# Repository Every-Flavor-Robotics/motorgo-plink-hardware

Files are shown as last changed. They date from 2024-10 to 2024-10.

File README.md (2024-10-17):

# MotorGo Plink
## The aim of this project is to make a 4 DC motor drive compatible with the motorgo ecosystem - specifically designed for beginner roboticists.  It should be the form factor of a pihat, but capable of operating entirely on it's own as well. Currently testing release version 1.0!
plink

### Feature list:
- Esp32s3 with Wifi and BT connectivity
- Form factor of a PiHat (we do not currently have the EEPROM requirements of the PiHat Spec)
- DC barrel jack and on-board buck from 6-17V into 5.1V up to 6A  (enough to power pi4 and pi5)
- 9 dof IMU  (LSM6DSOTR-C accel and gyro  +  LIS3MDLTR mag)
- USB-C programming compatible with arduino IDE
- Qwiic port x2 for easy integration with sensors
- Full gpio breakout on 40Pin header + full RPi GPIO passthrough if using as a hat
- 4 bidirectional DC motor channels up to 2A each channel
- 4 Encoder ports for use with EncoderGo 5pin jst for close loop feedback on each motor

### Schematics: 
- Top level


- Motor drivers


- IMU 


- Power system 


- connectors 


### Layout:
- Top - signals components and power


- Inner 1 - GND (I left faint top layer to show ground relative to traces)


- Inner 2 - GND and a tiny tiny power traces where needed


- Bottom - signals and power


- Dimensions


- Full




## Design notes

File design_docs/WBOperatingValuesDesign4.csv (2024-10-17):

Name | Value | Category | Description
Phase Marg | 59.51 ° | System Information | Bode Plot Phase Margin
Cross Freq | 55.92 kHz | System Information | Bode plot crossover frequency
Low Freq Gain | 72.57 dB | System Information | Gain at 1Hz
Gain Marg | -24.05 dB | System Information | Bode Plot Gain Margin
Vout | 5.09 V | System Information | Operational Output Voltage
IC Tolerance | 8 mV | IC | IC Feedback Tolerance
Cin IRMS | 2.79 A | Capacitor | Input capacitor RMS ripple current
Cin Pd | 2.59 mW | Capacitor | Input capacitor power dissipation
Cout IRMS | 371.57 mA | Capacitor | Output capacitor RMS ripple current
Cout Pd | 419.29 µW | Capacitor | Output capacitor power dissipation
Duty Cycle | 31.42% | System Information | Duty cycle
Efficiency | 90.5% | System Information | Steady state efficiency
Frequency | 881.05 kHz | System Information | Switching frequency
IC Tj | 112.33 °C | IC | IC junction temperature
ICThetaJA | 32 °C/W | IC | IC junction-to-ambient thermal resistance
L Ipp | 1.29 A | Inductor | Peak-to-peak inductor ripple current
L Pd | 630 mW | Inductor | Inductor power dissipation
IC Pd | 2.57 W | IC | IC power dissipation
Pout | 30.53 W | System Information | Total output power
Iin Avg | 1.98 A | IC | Average input current
IC Ipk | 6.64 A | IC | Peak switch current in IC
Mode | CCM | System Information | Conduction Mode
Vout p-p | 9.74 mV | System Information | Peak-to-peak output ripple voltage
M Irms | 3.36 A | Mosfet | MOSFET RMS current
Vout Ripple requirement used for Cout calculations | 3.00% | System Information | Custom maximum output ripple requirement that was used for Cout selection(% of Vout).
Vin p-p | 245.24 mV | System Information | Peak-to-peak input voltage
Vin Ripple requirement used for Cin calculations | 5.00% | System Information | Custom maximum input ripple requirement that was used for Cin selection(% of Minimum Vin).
Overshoot Value | 93.14 mV | System Information | Theoretical Vout Overshoot Value
Undershoot Value | 115.92 mV | System Information | Theoretical Vout Undershoot Value
Vout transient requirement used for Cout calculations | 5.00% | System Information | Custom Transient voltage change requirement that was used for Cout selection (% of Vout).
Iout transient step used for Cout calculations | 3 A | System Information | Custom Transient current step requirement that was used for Cout selection (A).
Minimum Cout required for stability | 17.75 uF | System Information | Minimum Cout required for stability
IC Iq Pd | 10.2 mW | IC | IC Iq Pd
Total Pd | 3.21 W | Power | Total Power Dissipation
FootPrint | 622 mm² | System Information | Total Foot Print Area of BOM components
Vin | 17 V | System Information | Vin operating point
Iout | 6 A | System Information | Iout operating point
Cin Pd | 2.59 mW | Power | Input capacitor power dissipation
Cout Pd | 419.29 µW | Power | Output capacitor power dissipation
L Pd | 630 mW | Power | Inductor power dissipation
IC Pd | 2.57 W | Power | IC power dissipation
Vout Actual | 5.09 V | System Information | Vout Actual calculated based on selected voltage divider resistors
Vout Tolerance | 2.72% | System Information | Vout Tolerance based on IC Tolerance (no load) and voltage divider resistors if applicable
Total BOM | $4.91 | System Information | Total BOM Cost
BOM Count | 17 | System Information | Total Design BOM count

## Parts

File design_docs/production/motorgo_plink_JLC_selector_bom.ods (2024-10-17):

Comment | topDesignator | bottomDesignator | Footprint | JLCPCB Part #
3.92k | R19 |  | Resistor_SMD:R_0402_1005Metric | C3013164
.022uF | C13,C5,C9 |  | Capacitor_SMD:C_0402_1005Metric | C1532
22uF16v | C24,C25 |  | Capacitor_SMD:C_0603_1608Metric | C2762594
0 | R6,R7 |  | Resistor_SMD:R_0402_1005Metric | C3017451
68pf | C1 |  | Capacitor_SMD:C_0201_0603Metric | C3833199
6.8nf | C20 |  | Capacitor_SMD:C_0201_0603Metric | C505476
BM05B-SRSS-TB_LF__SN_ | J14,J18,J16,J20 |  | SnapEDALibrary:JST_BM05B-SRSS-TB_LF__SN_ | C265092
53.6k | R24 |  | Resistor_SMD:R_0402_1005Metric | C2998086
47uF3mOhm | C23 |  | Capacitor_SMD:C_1210_3225Metric | C7432791
220uF50v | C16 |  | Capacitor_SMD:CP_Elec_10x10 | C125977
10k | R14,R10,R13,R36,R11,R12,R15,R37 |  | Resistor_SMD:R_0402_1005Metric | C25744
36.5k | R17 |  | Resistor_SMD:R_0402_1005Metric | C25887
LED | D2 |  | LED_SMD:LED_0805_2012Metric | C84260
TPS54620RHLR | U6 |  | LCSC_parts:VQFN-14_L3.5-W3.5-P0.50-TL-EP_TPS54622RHLT | C263274
USBLC6-2P6 | U2 |  | Package_TO_SOT_SMD:SOT-666 | C2827693
LED | D1 |  | LED_SMD:LED_0805_2012Metric | C84259
LED | D3 |  | LED_SMD:LED_0805_2012Metric | C84256
Conn_01x02_Pin | J8,J10,J22,J6 |  | Connector_Molex:Molex_KK-254_AE-6410-02A_1x02_P2.54mm_Vertical | C722716
4.7uF1mOhm | C17 |  | Capacitor_SMD:C_0603_1608Metric | C268021
tact_switch | J2,J3 |  | Button_Switch_SMD:SW_SPST_TL3342 | C2886897
ESP32-S3-WROOM-1 | U1 |  | mg_mini_v1r3:ESP32-S3-WROOM-1 | C2913198
DRV8874PWPR | U3,U9,U4,U5 |  | LCSC_parts:HTSSOP-16_L5.0-W4.4-P0.65-LS6.4-BL-EP | C1855818
LSM6DS3TR | U11 |  | LCSC_parts:LSM6DSOTR_LGA-14 | C967633
20k | RMODE3,RMODE2,RMODE1,RMODE4 |  | Resistor_SMD:R_0402_1005Metric | C3017501
10k | R25 |  | Resistor_SMD:R_0402_1005Metric | C2906885
.022uF | C28 |  | Capacitor_SMD:C_0402_1005Metric | C380305
1k | R50,R1,R49,R3,R46,R2 |  | Resistor_SMD:R_0402_1005Metric | C11702
2.2uH12.7mOhm | L1 |  | kicad_lceda:IND-SMD_L6.6-W6.4_CKSTT0610 | C5440776
100nF | C31,C22,C30 |  | Capacitor_SMD:C_0402_1005Metric | C880603
I2C_STANDARDQWIIC | J15,J13 |  | Connector_JST:JST_SH_BM04B-SRSS-TB_1x04-1MP_P1.00mm_Vertical | C495539
5k1 | R33,R31,R32,R9,R30,R4,R5,R8 |  | Resistor_SMD:R_0402_1005Metric | C25905
2k | R39,R38 |  | Resistor_SMD:R_0402_1005Metric | C4109
Conn_02x20_Odd_Even | J4 | J7 | Connector_PinSocket_2.54mm:PinSocket_2x20_P2.54mm_Vertical_SMD | C3975165
4.7uF1mOhm | C2,C19,C15 |  | Capacitor_SMD:C_0805_2012Metric | C440198
AMS1117-3.3 | U8 |  | Package_TO_SOT_SMD:SOT-223-3_TabPin2 | C347222
53.6k | R18 |  | Resistor_SMD:R_0402_1005Metric | C5153961
102k | R16 |  | Resistor_SMD:R_0402_1005Metric | C2933066
2.2nF0Ohm | C18 |  | Capacitor_SMD:C_0201_0603Metric | C5142540
1uF | C32 |  | Capacitor_SMD:C_0603_1608Metric | C15849
DC_Barrel | J11 |  | LCSC_parts:CONN-TH_DC-005-2.5A-2.0 | C84007
USB4520-03-0-A_REVA | J1 |  | mg_mini_v1r3:USB-C-SMD_TYPEC-303-ACP16 | C720628
100uF | C10,C6,C29,C14 |  | Capacitor_SMD:C_1210_3225Metric | C6120014
0.1uF | C26,C27,C11,C3,C4,C7,C12,C8 |  | Capacitor_SMD:C_0402_1005Metric | C307331
4.87k | RP1,RP4,RP3,RP2 |  | Resistor_SMD:R_0402_1005Metric | C3015971

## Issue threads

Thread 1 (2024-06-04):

Footprints wrong in BOM

alexchunlin, 2024-06-04:
R34 is the 0R0 to bridge the island of the IMU to the rest of the board and is selected as a 0402 resistor when the footprint is an 0603.
LCSC part number should be C3016185 or equivalent 0603 0Ohm resistor

J15, J17, J13, J19 are all the qwiic connectors and have vertical footprints, but the components chosen were for horizontal form.
LCSC part number should be C160390 - Part number: BM04B-SRSS-TB(LF)(SN)

Closed 2024-10-17.

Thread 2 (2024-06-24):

Pull nSleep HIGH on DRV8874

SwapnilPande, 2024-06-24:
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

Currently, nSleep is floating, it needs to be pulled HIGH to enable the motor controller

Closed 2024-10-17.

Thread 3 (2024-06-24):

IMU circuit errors

SwapnilPande, 2024-06-24:
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
* SDA/SCL switched for Magnetometer

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

Closed 2024-10-17.

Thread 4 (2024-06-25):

Raspberry Pi Pin headers are mirrored

SwapnilPande, 2024-06-25:

Closed 2024-10-17.

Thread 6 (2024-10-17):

add remove soldermask from around the mounting holes

alexchunlin, 2024-10-17:
Bottom of board has soldermask all the way up to the board holes.  It should match the design of the front of the board, where it is removed in a 5mm Diameter concentric on the hole.

alexchunlin, 2024-11-11:
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

bottom side matches now in diode rework branch

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

Closed 2024-11-11.

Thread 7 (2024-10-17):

sourcing 2x2 magnetometer challenges

alexchunlin, 2024-10-17:
the magnetometer chosen is not easy to source and might be considered to swap for a similar chip

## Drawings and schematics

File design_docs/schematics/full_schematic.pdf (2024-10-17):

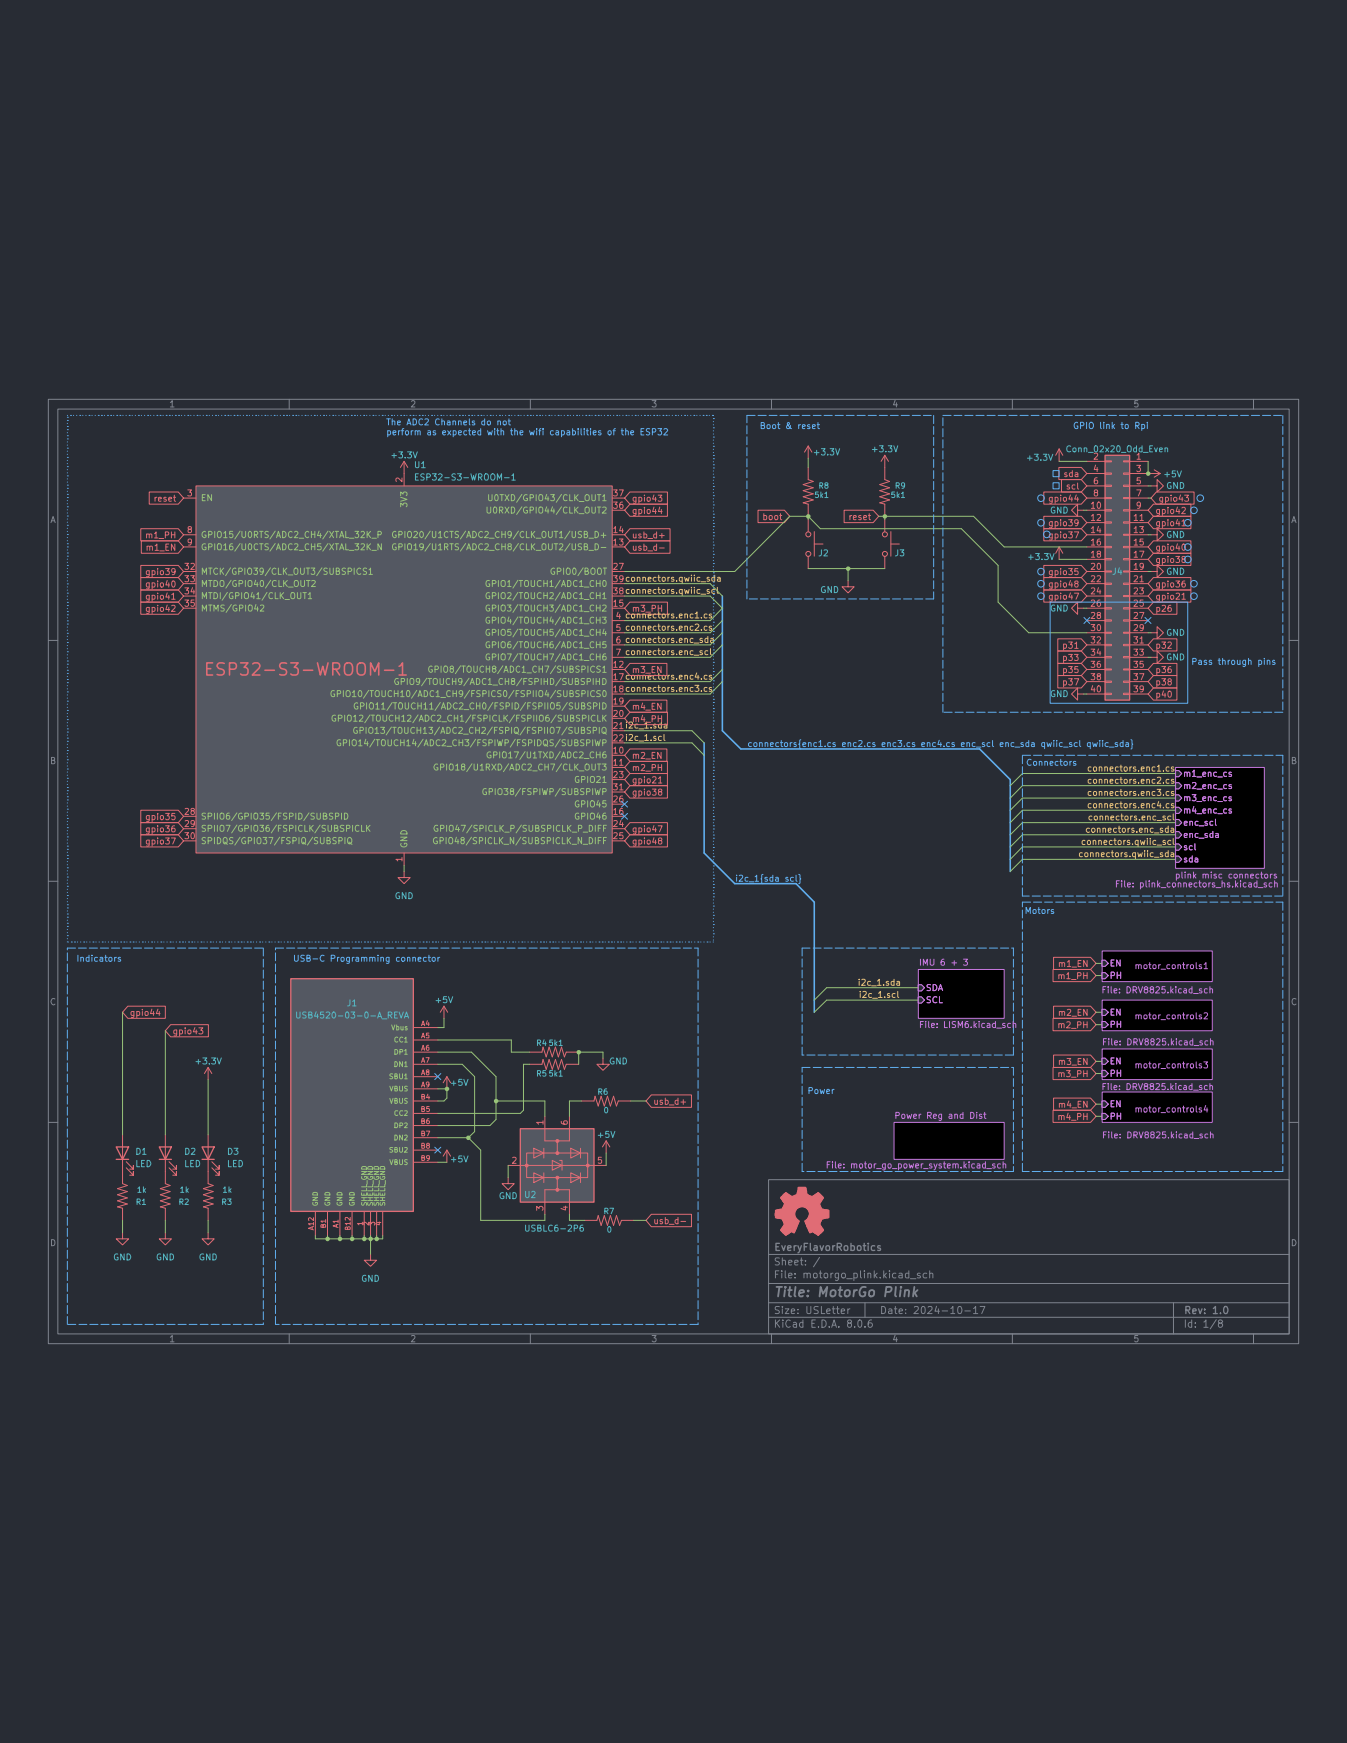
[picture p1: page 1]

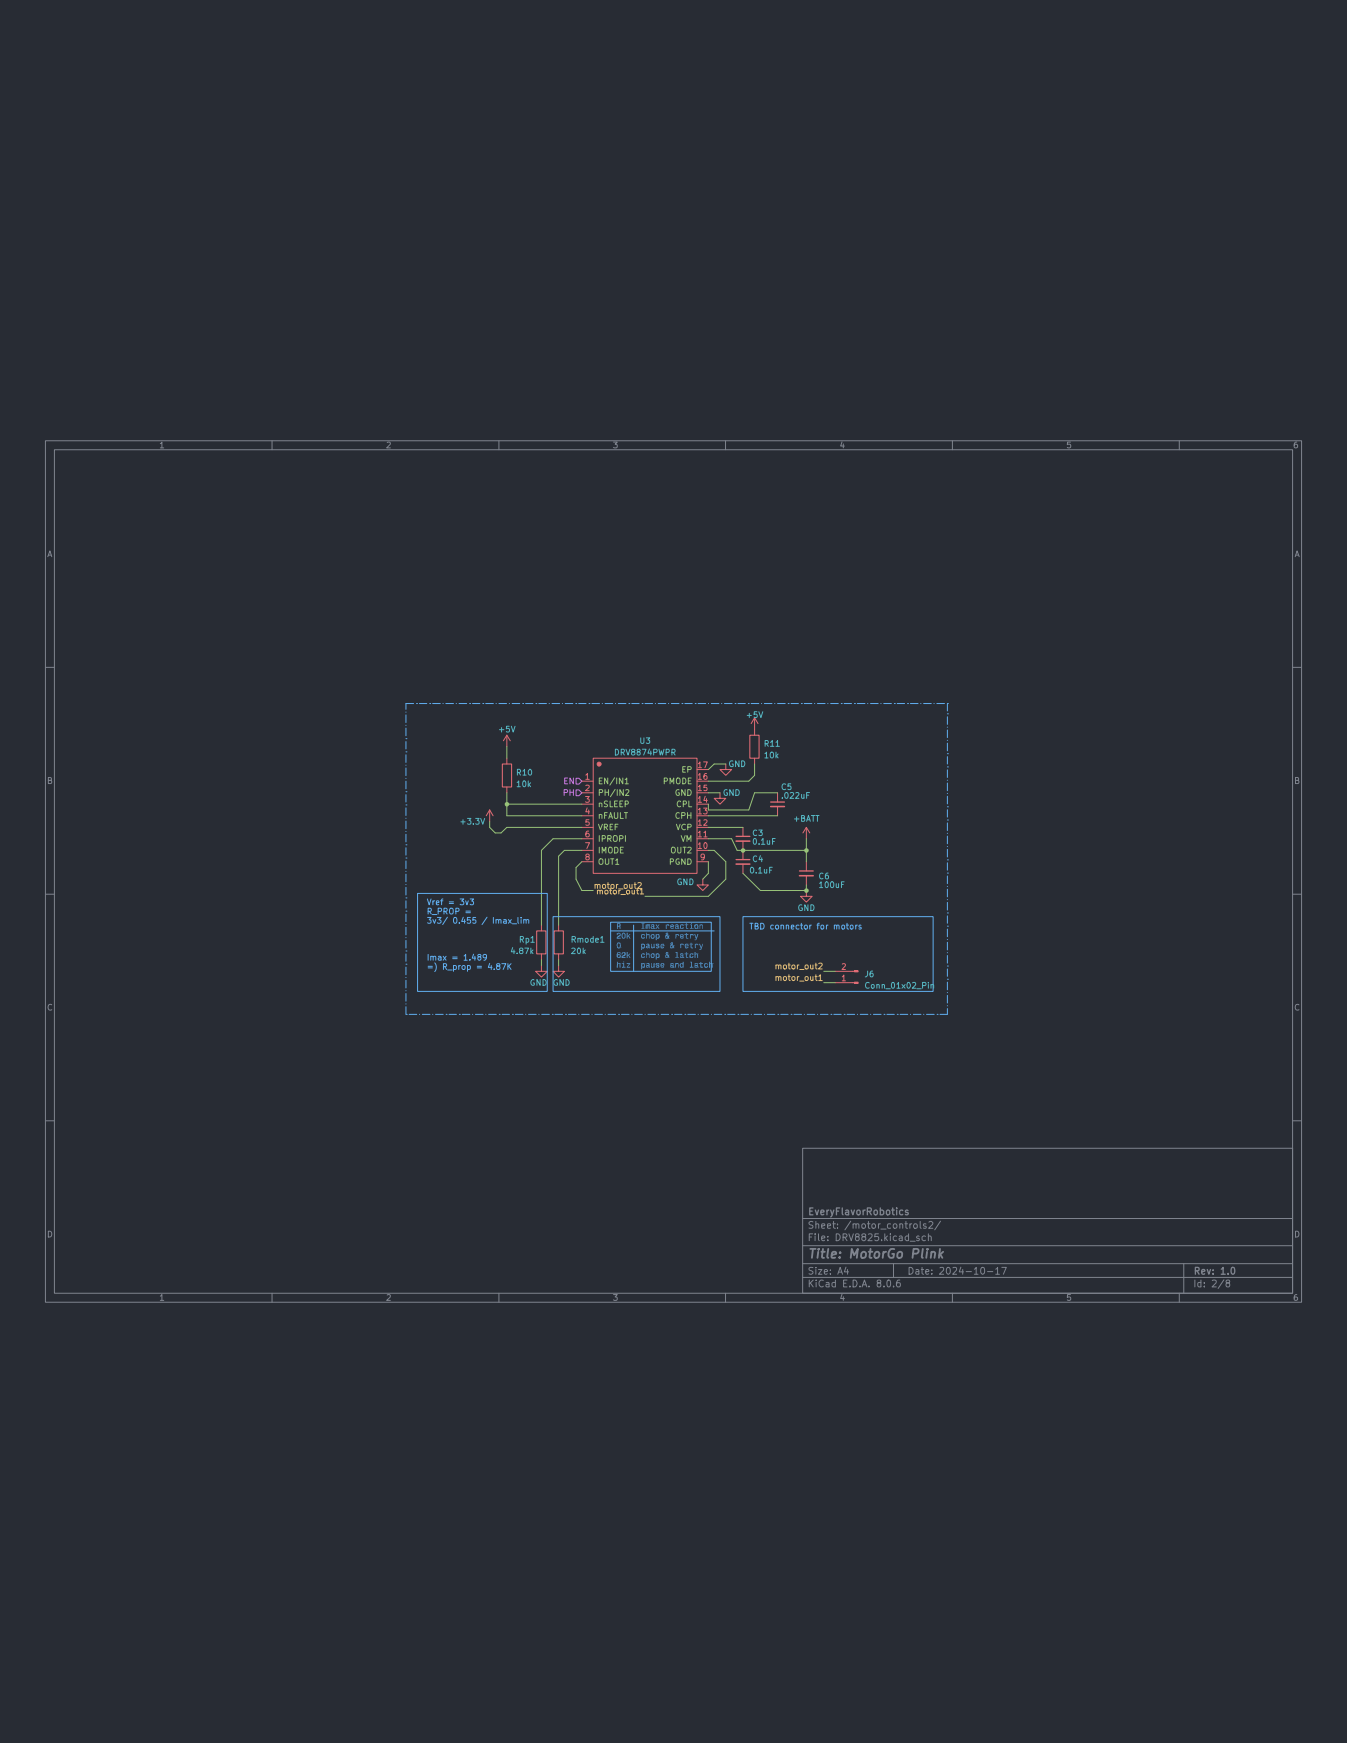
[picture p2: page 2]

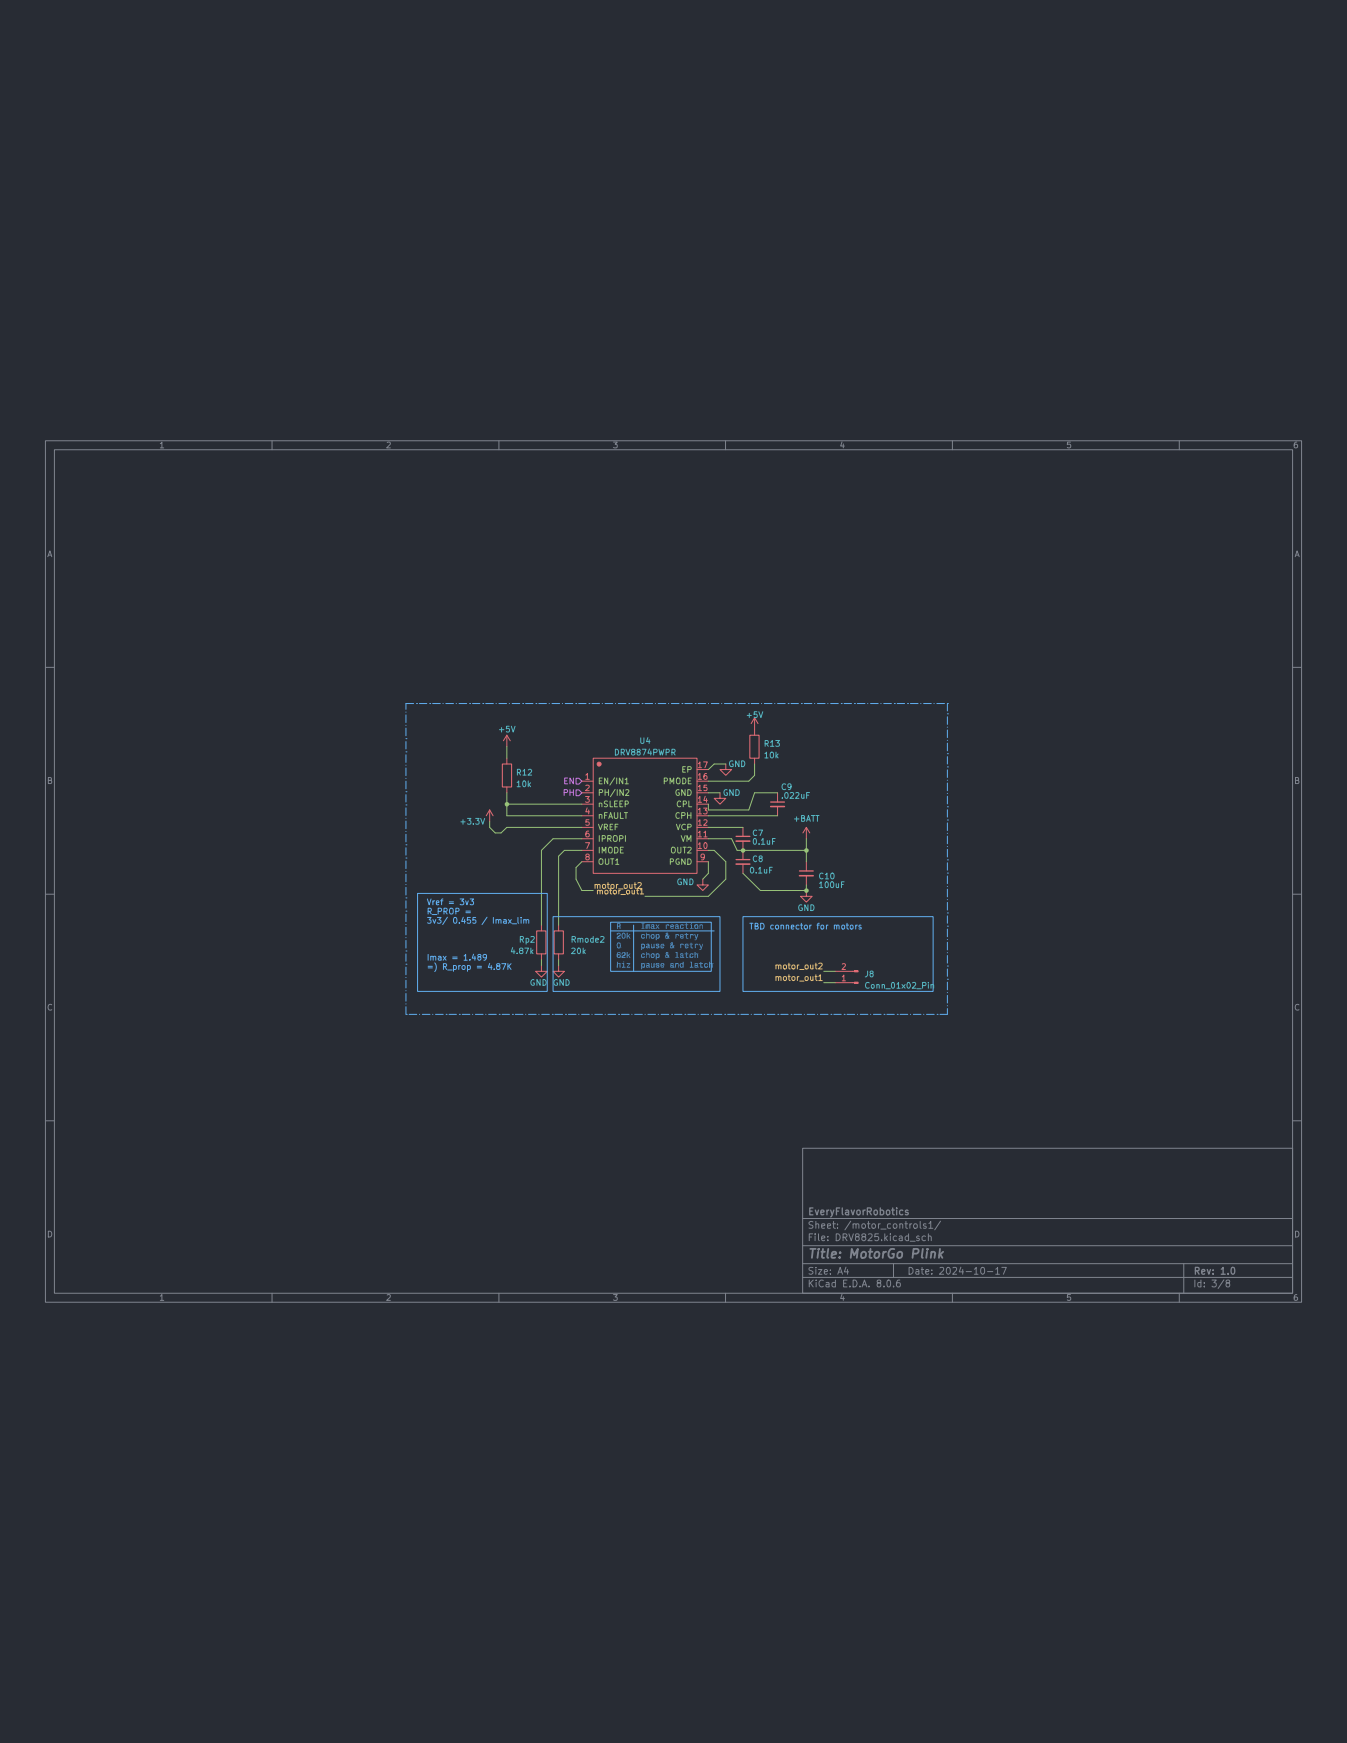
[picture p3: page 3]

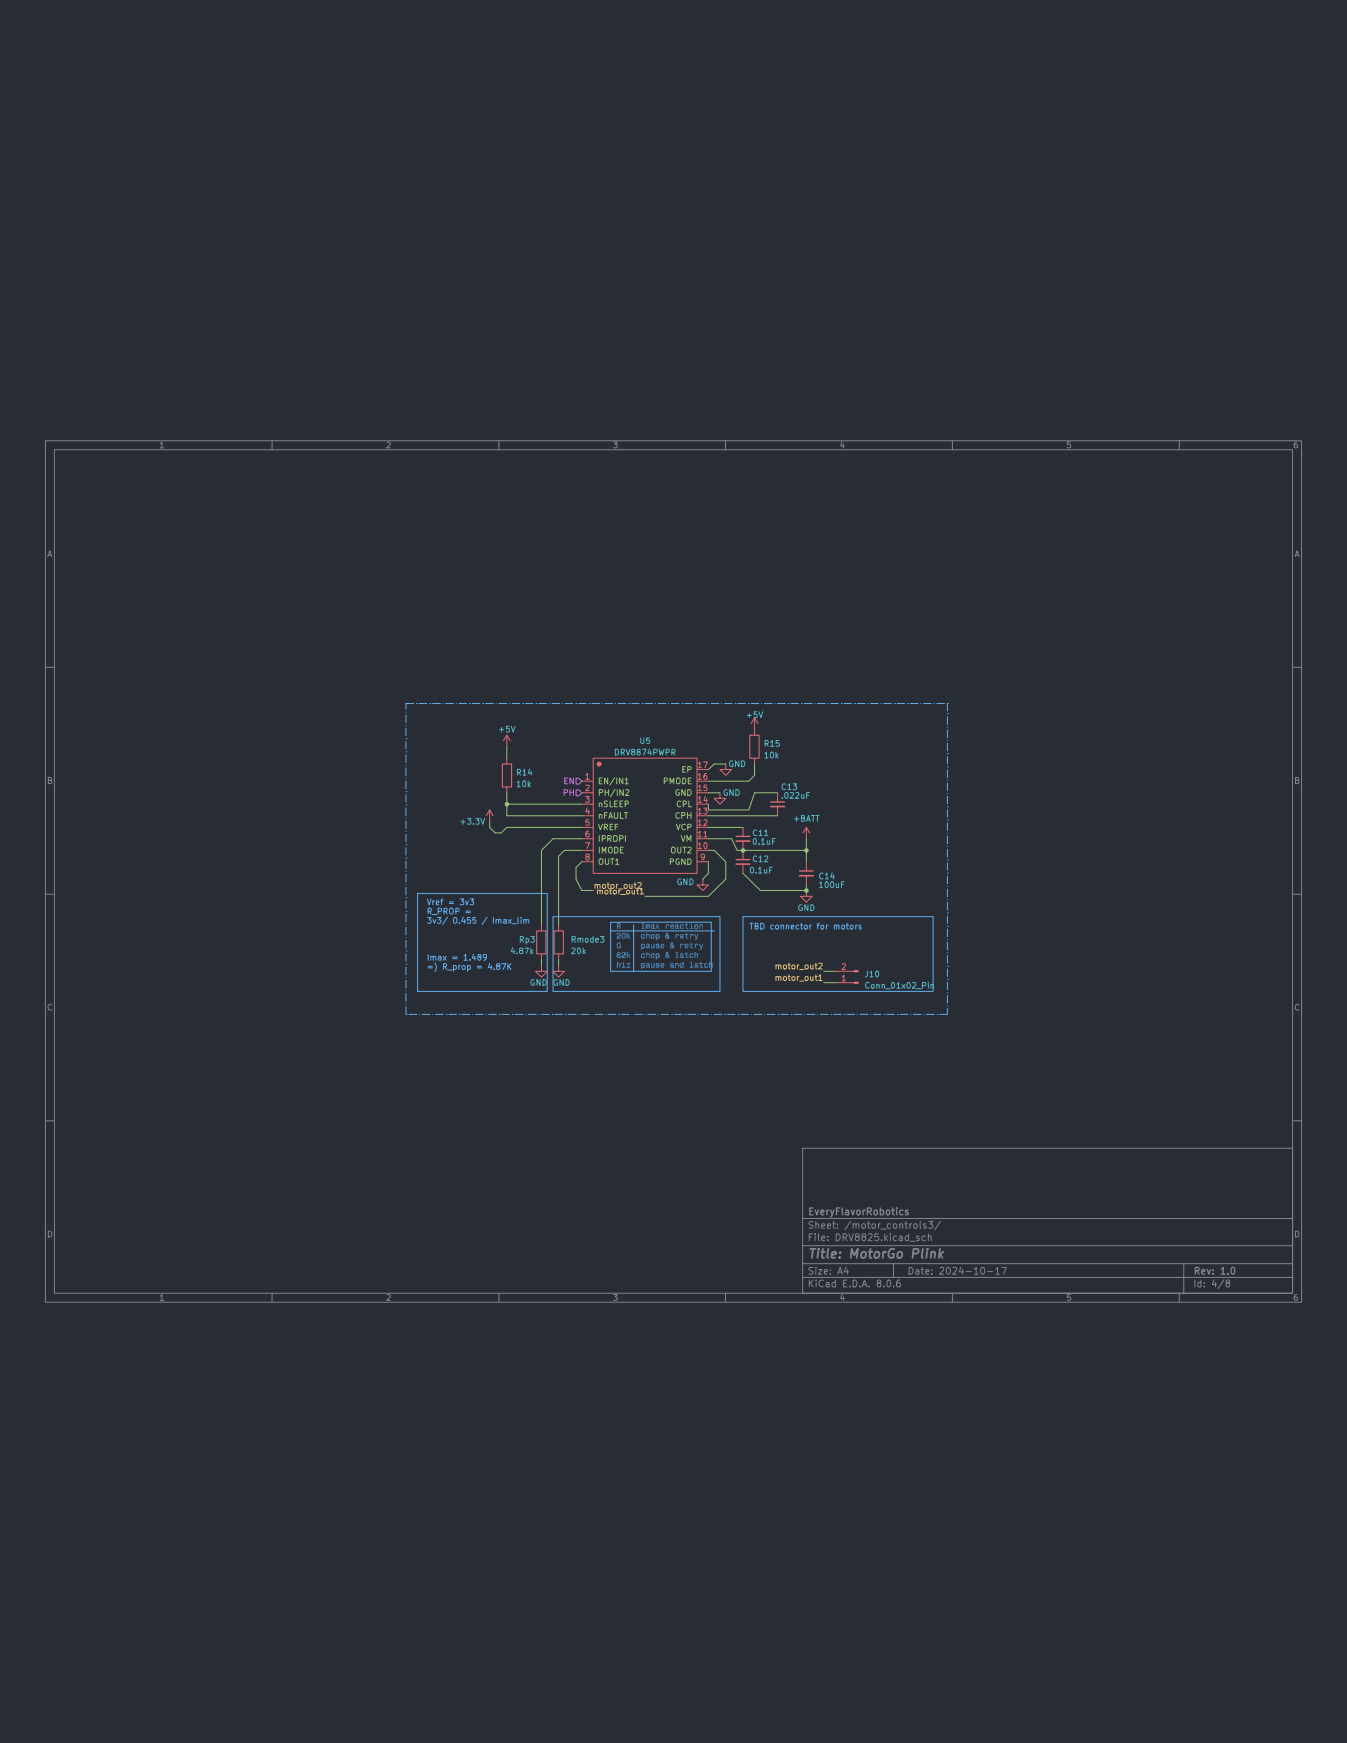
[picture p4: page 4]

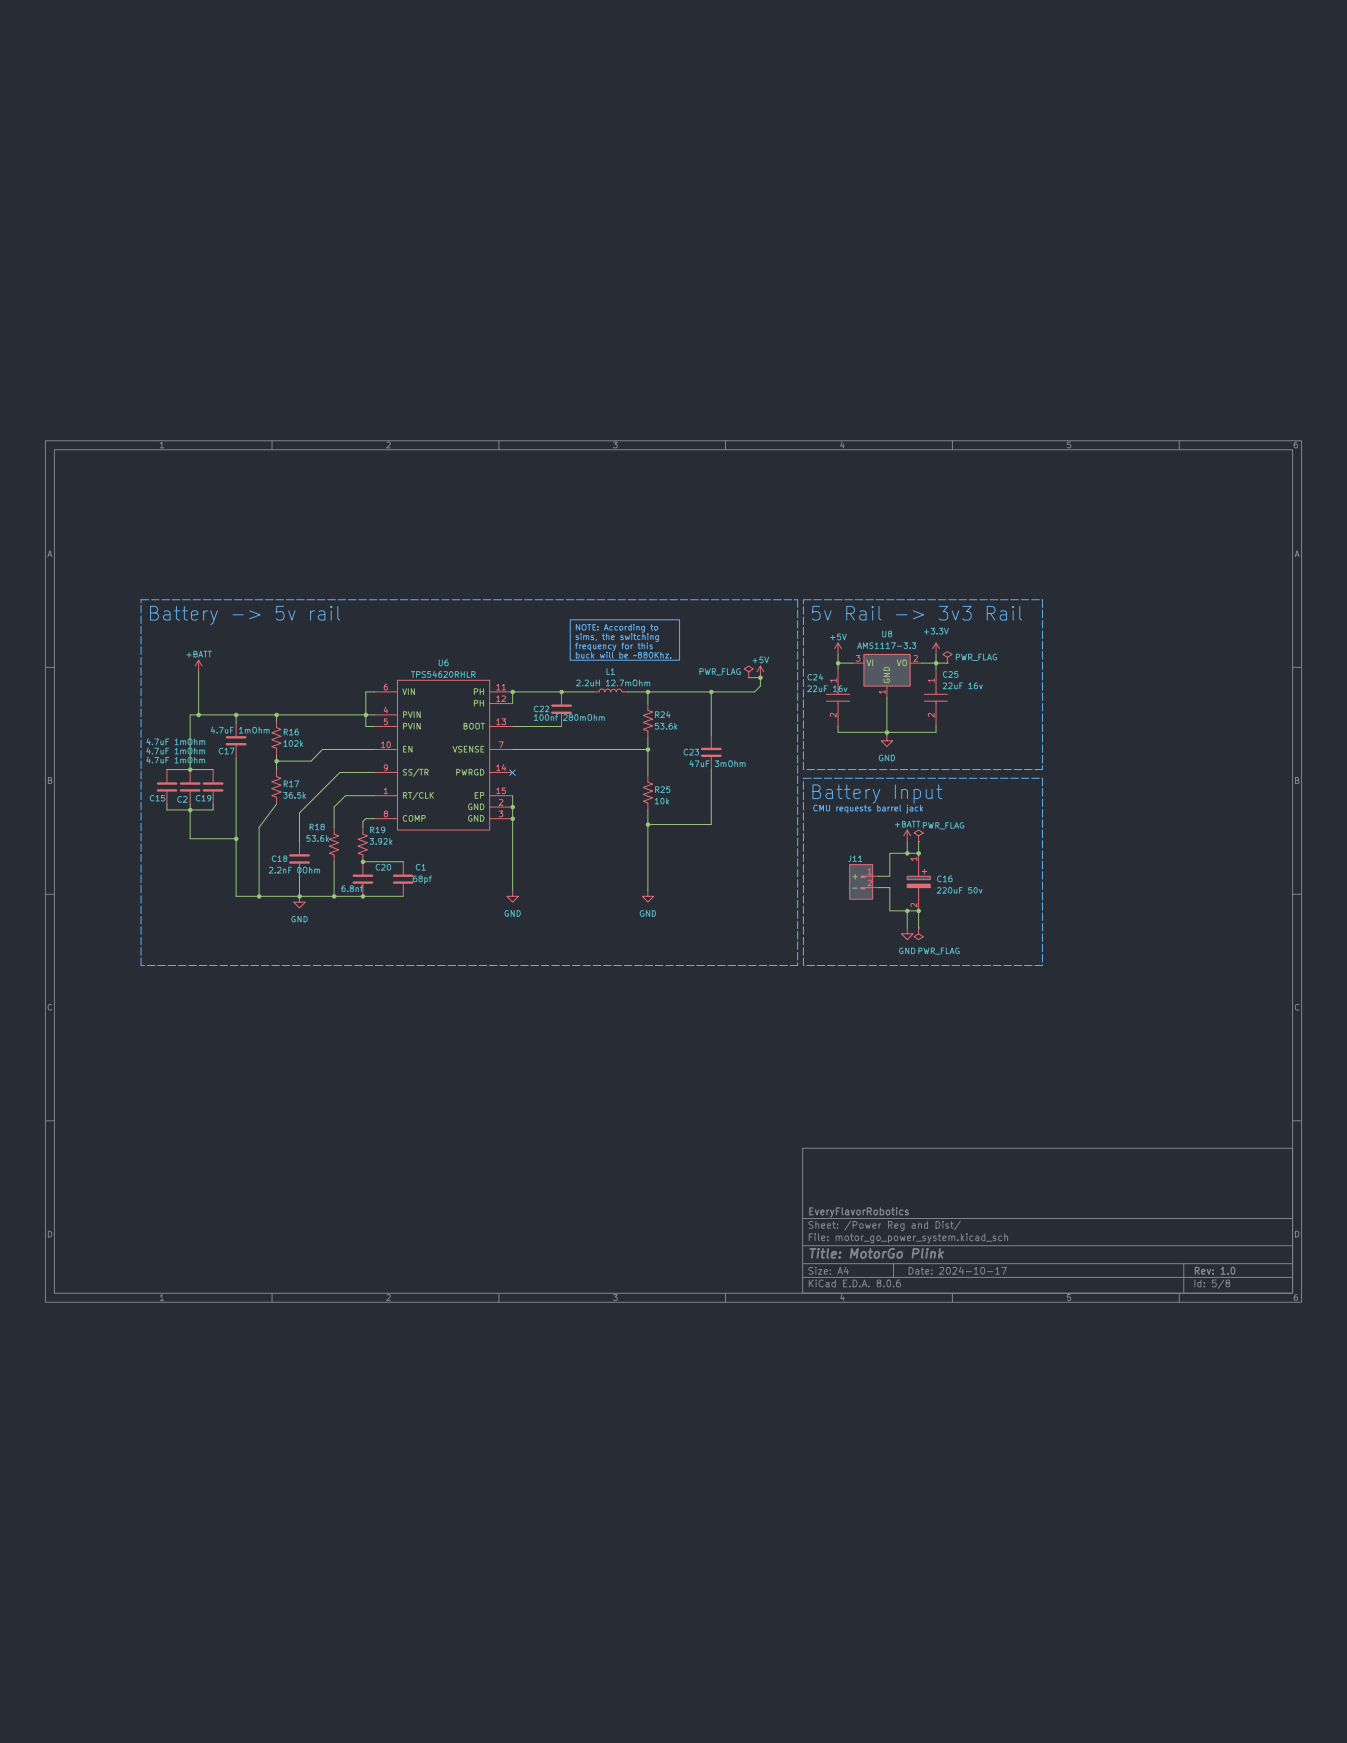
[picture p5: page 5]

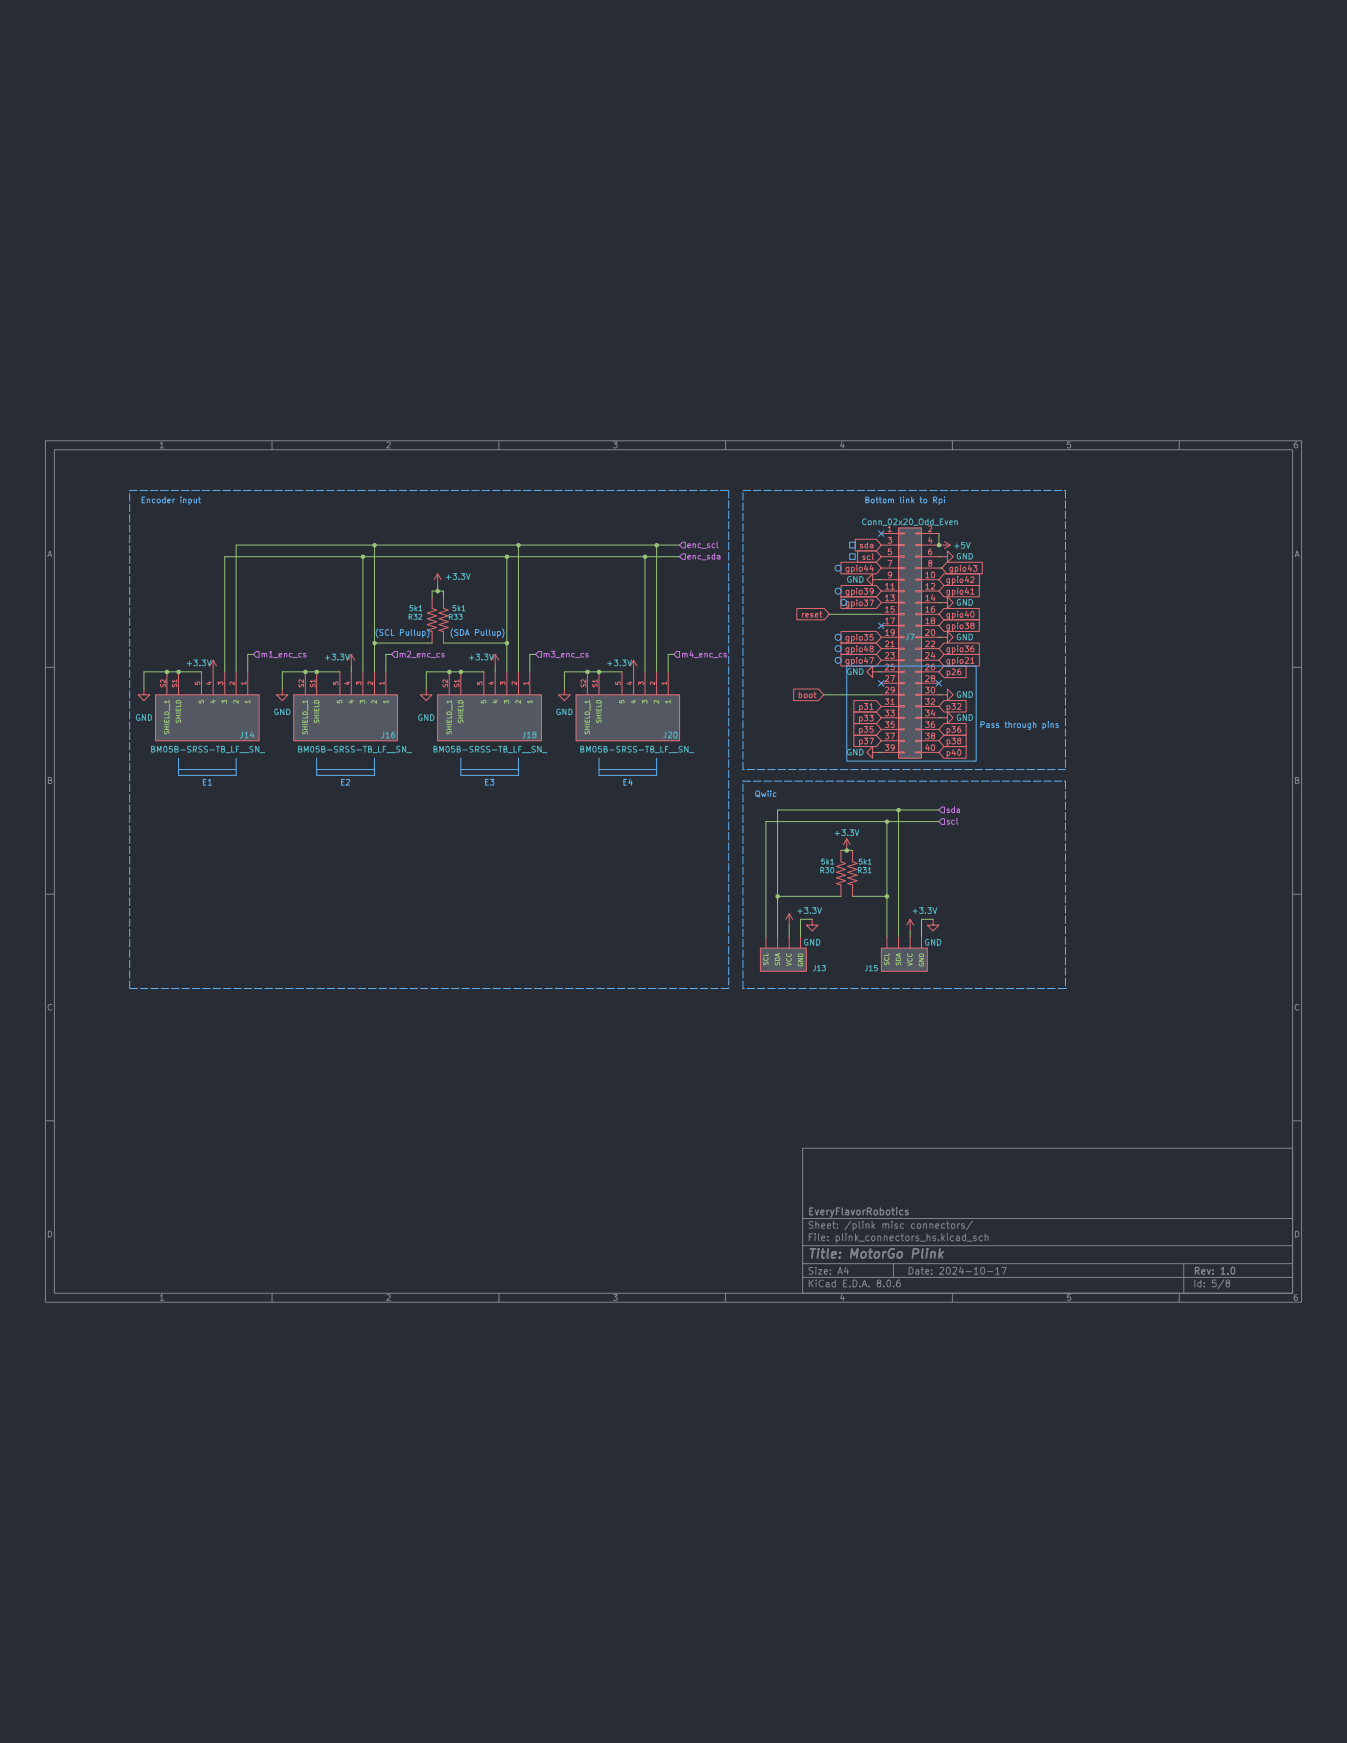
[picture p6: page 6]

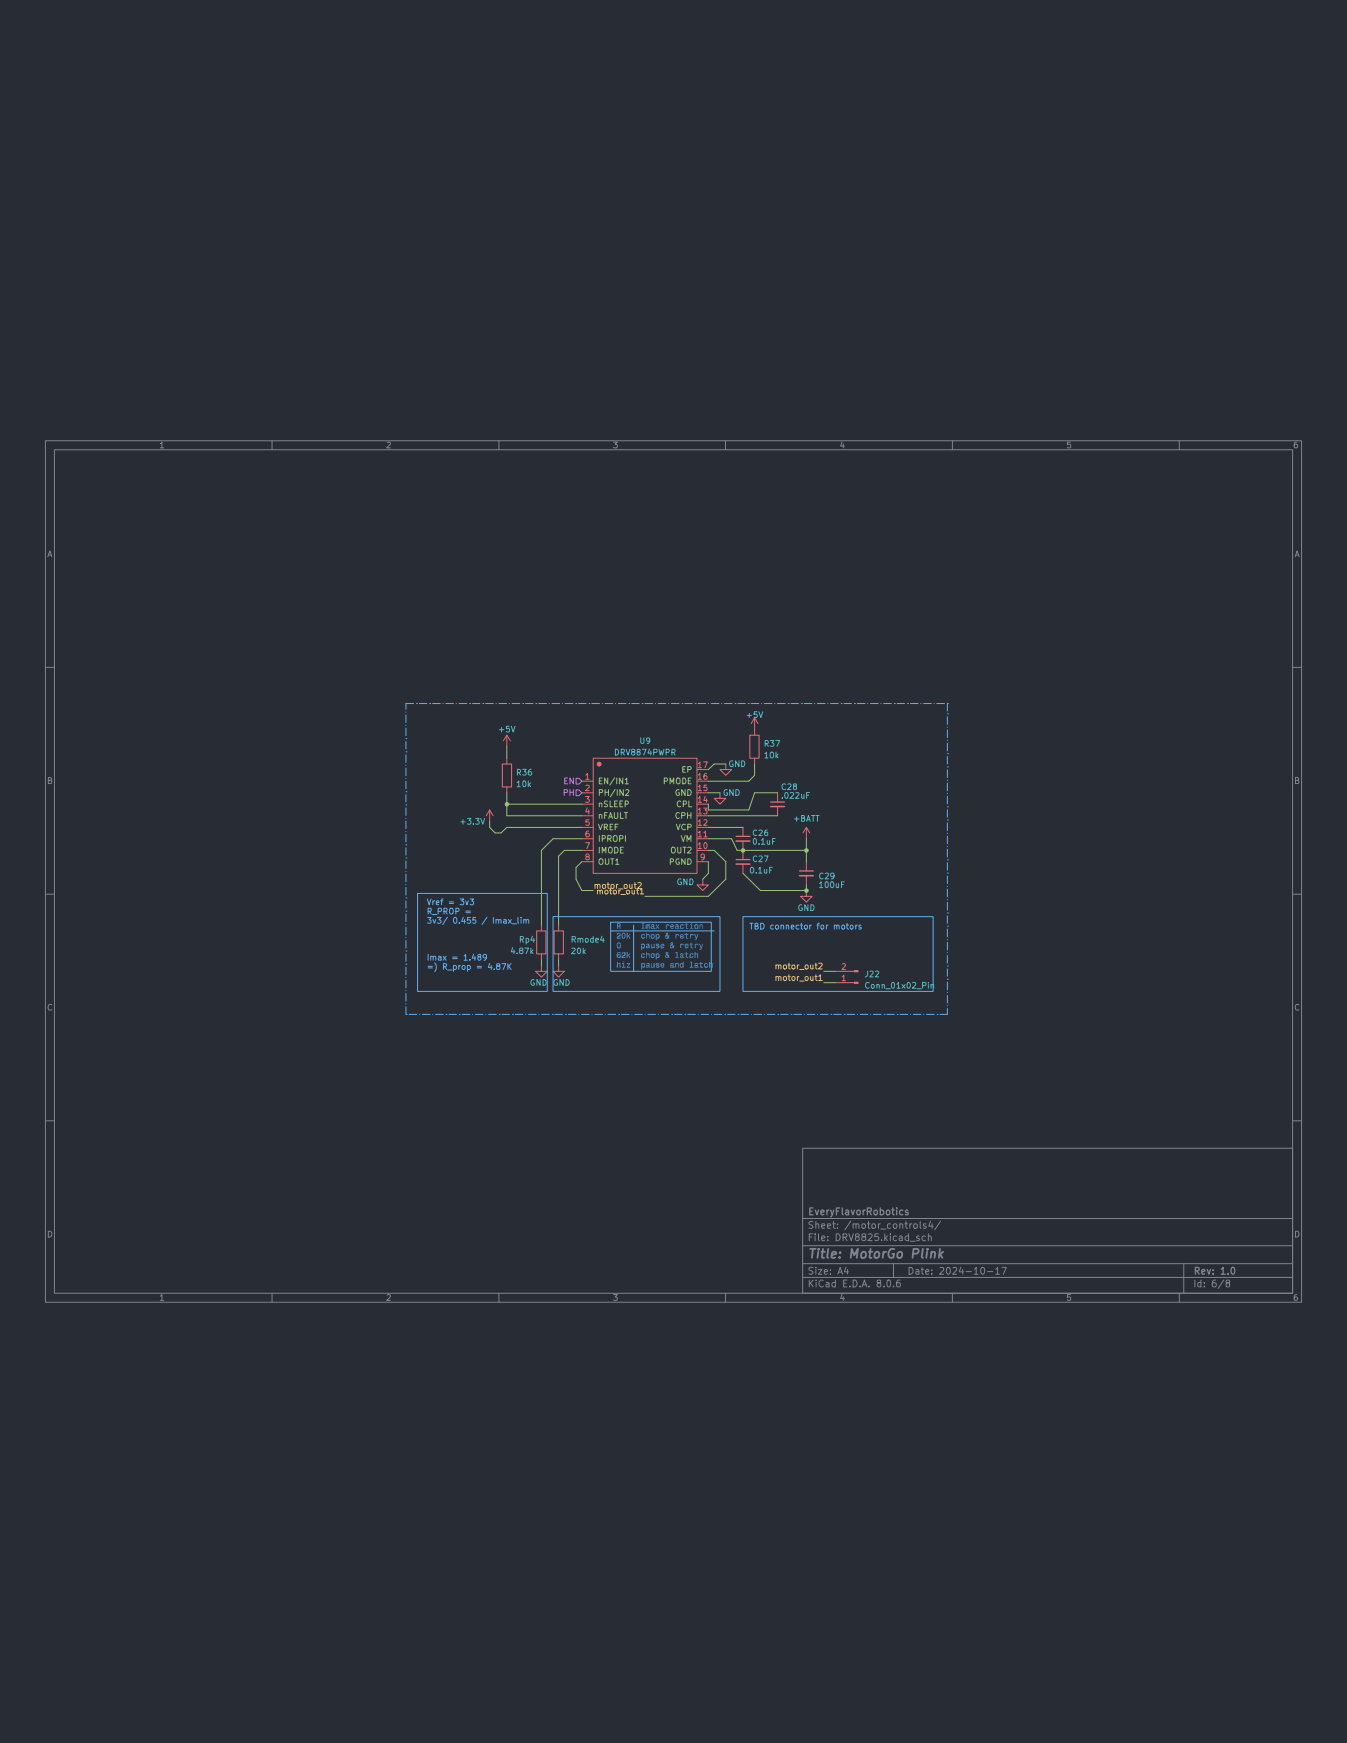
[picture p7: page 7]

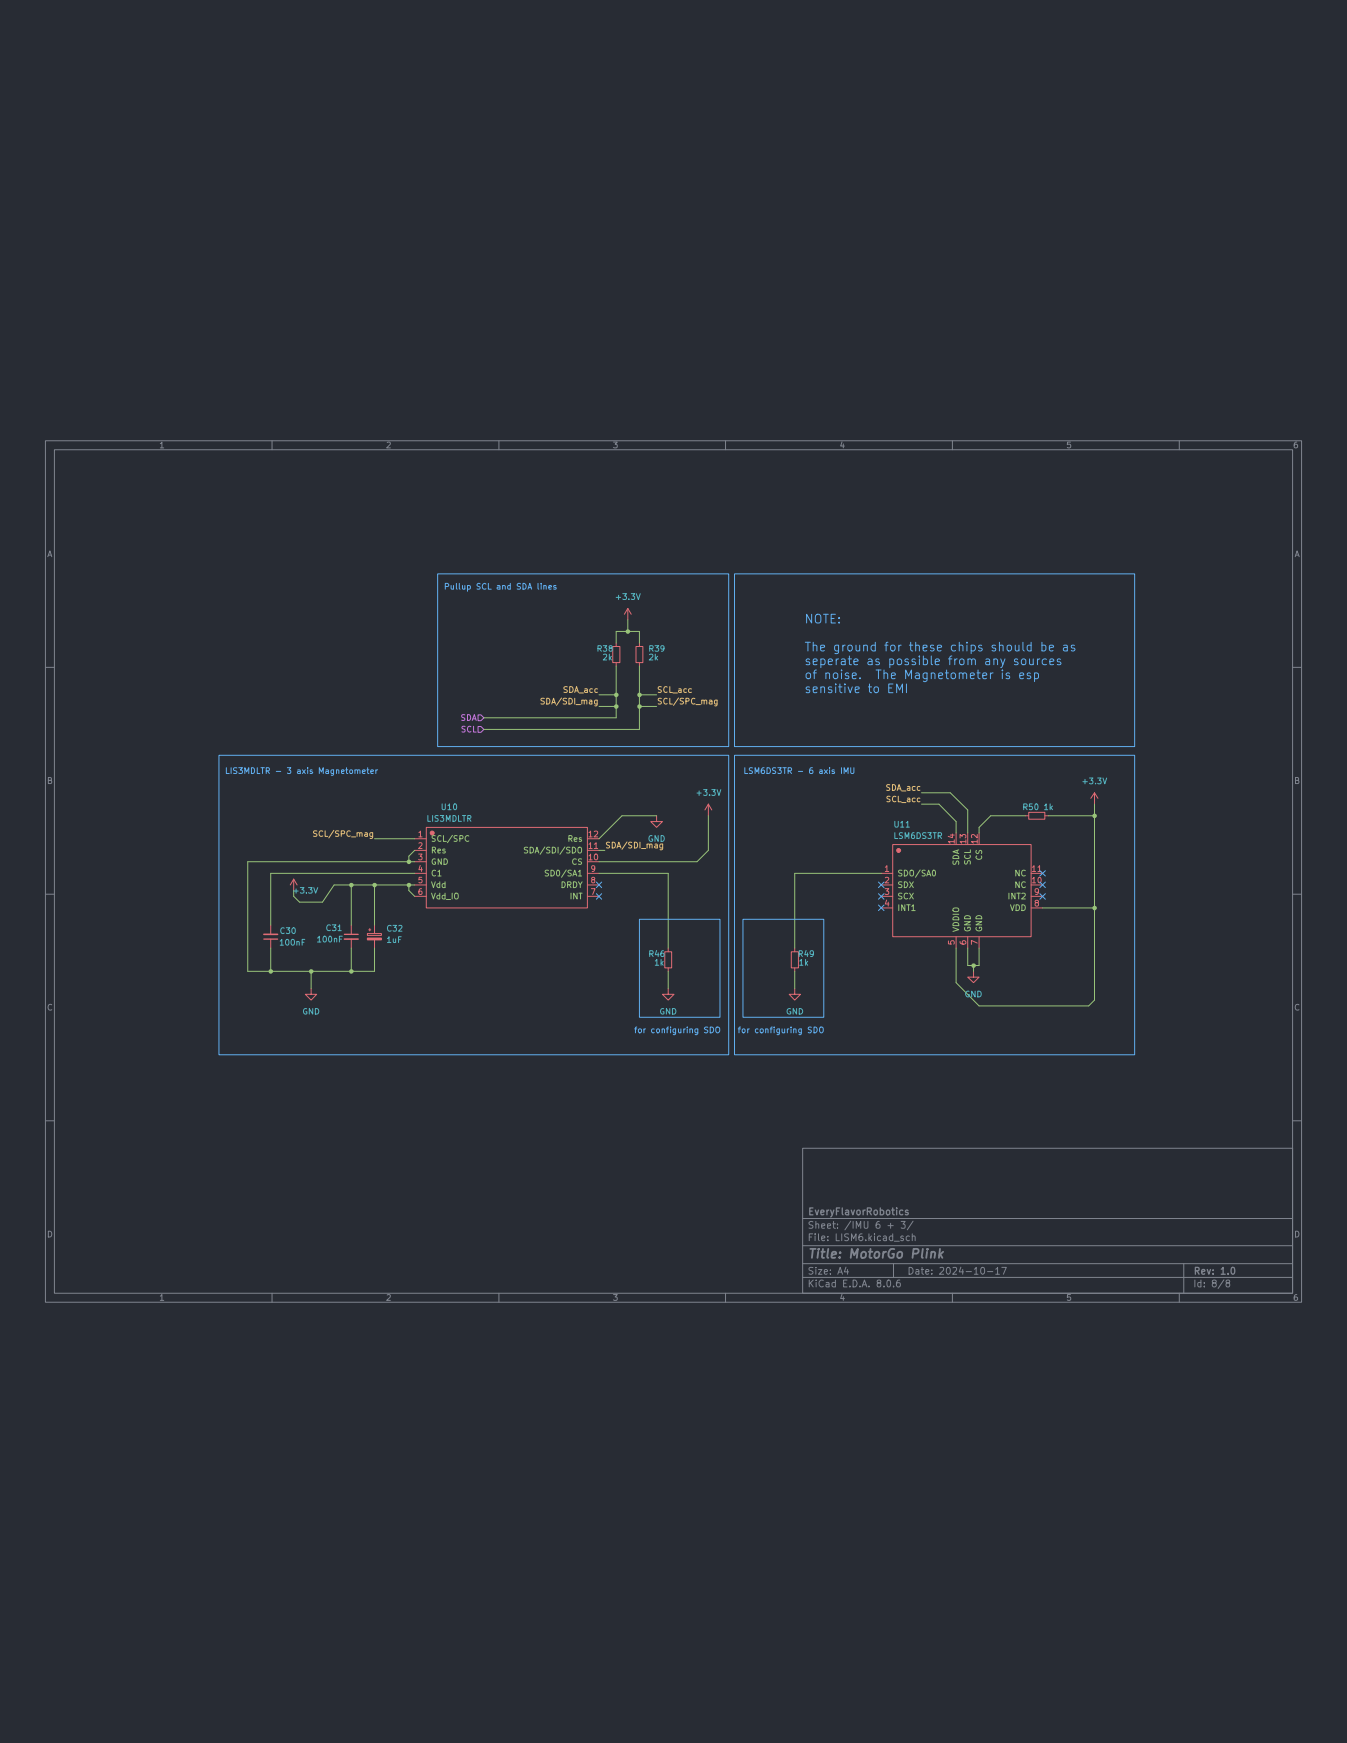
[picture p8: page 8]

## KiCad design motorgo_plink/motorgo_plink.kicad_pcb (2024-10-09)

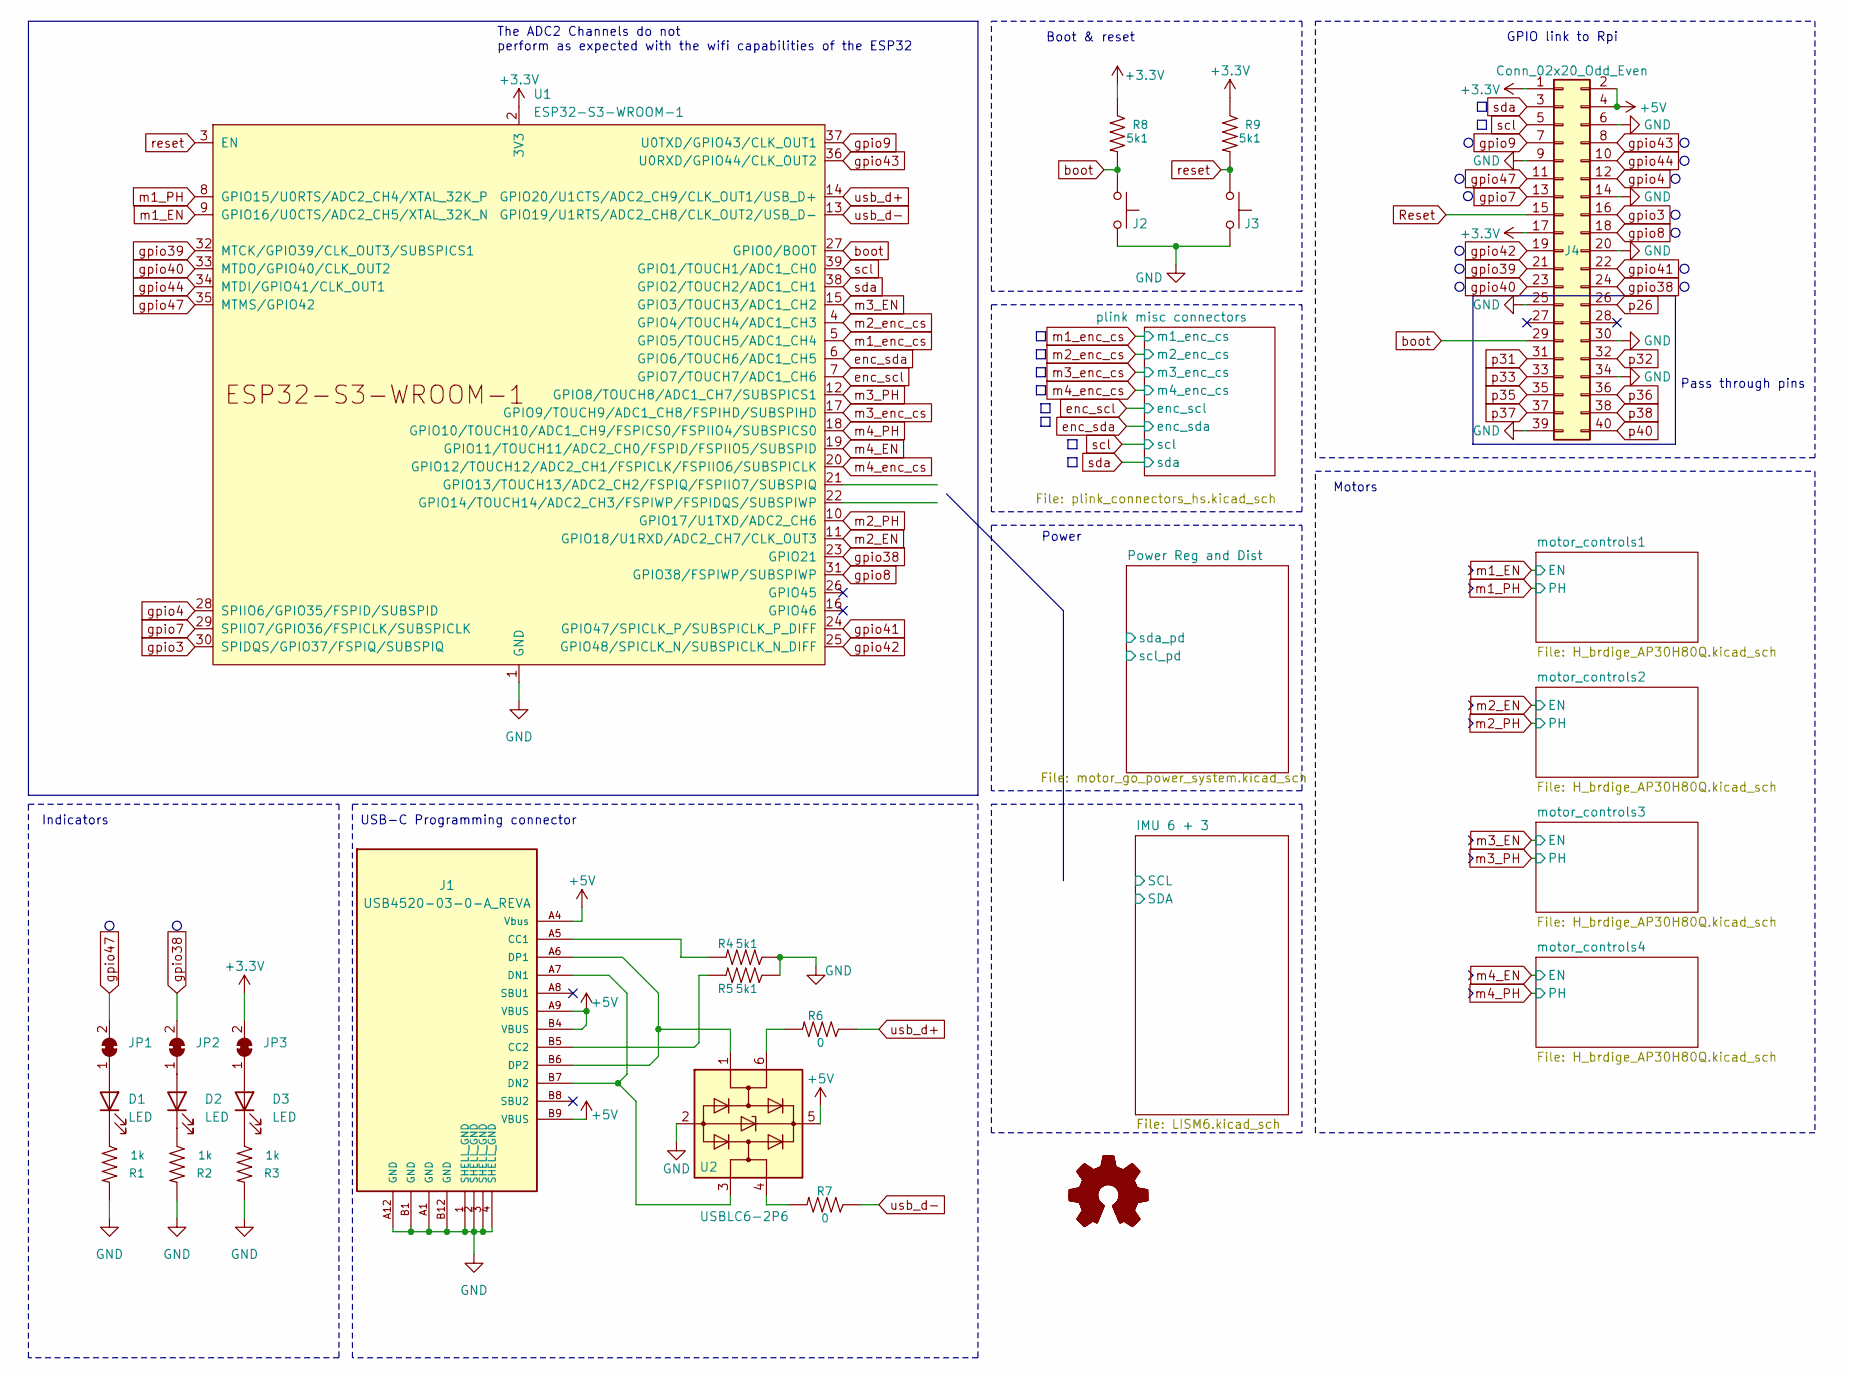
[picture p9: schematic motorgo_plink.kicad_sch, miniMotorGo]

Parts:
D1: LED; LED_0805_2012Metric; LCSC_Part_Number C84259
D2: LED; LED_0805_2012Metric; LCSC_Part_Number C84260
D3: LED; LED_0805_2012Metric; LCSC_Part_Number C84256
J1: USB4520-03-0-A_REVA; USB-C-SMD_TYPEC-303-ACP16; LCSC_Part_Number C720628
J2, J3: SW_SPST_TL3342; LCSC_Part_Number C2886897
J4: Conn_02x20_Odd_Even; PinSocket_2x20_P2.54mm_Vertical_SMD; LCSC_Part_Number C3975165
JP1, JP2, JP3: DNP; SolderJumper-2_P1.3mm_Open_RoundedPad1.0x1.5mm
R1, R2, R3: 1k; R_0402_1005Metric; LCSC_Part_Number C2906899
R4, R5, R8, R9: 5k1; R_0402_1005Metric; LCSC_Part_Number C409700
R6, R7: 0; R_0402_1005Metric; LCSC_Part_Number C3017451
U1: ESP32-S3-WROOM-1; LCSC_Part_Number C2913198
U2: USBLC6-2P6; SOT-666; LCSC_Part_Number C2827693

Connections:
+3.3V: J4.1, J4.17, JP3.2 (B), R8.1, R9.1, U1.2 (3V3); also elsewhere on the board
+5V: J1.A4 (Vbus), J1.A9 (VBUS), J1.B4 (VBUS), J1.B9 (VBUS), J4.2, J4.4, U2.5 (VBUS); also elsewhere on the board
GND: J1.1 (SHELL_GND), J1.2 (SHELL_GND), J1.3 (SHELL_GND), J1.4 (SHELL_GND), J1.A1 (GND), J1.A12 (GND), J1.B1 (GND), J1.B12 (GND), J2.1, J3.2, J4.6, J4.9, J4.14, J4.20, J4.25, J4.30, J4.34, J4.39, R1.2, R2.2, R3.2, R4.1, R5.1, U1.1 (GND), U1.40 (GND), U1.41 (GND), U2.2 (GND); also elsewhere on the board
unnamed: D1.2 (A), JP1.1 (A)
unnamed: D1.1 (K), R1.1
unnamed: D2.2 (A), JP2.1 (A)
unnamed: D2.1 (K), R2.1
unnamed: D3.2 (A), JP3.1 (A)
unnamed: D3.1 (K), R3.1
unnamed: J1.A5 (CC1), R4.2
unnamed: J1.B5 (CC2), R5.2
unnamed: J1.A7 (DN1), J1.B7 (DN2), U2.3 (I/O2)
unnamed: J1.A6 (DP1), J1.B6 (DP2), U2.1 (I/O1)
unnamed: R6.2, U2.6 (I/O1)
unnamed: R7.2, U2.4 (I/O2)
Reset: J4.15; also elsewhere on the board
boot: J2.2, J4.29, R8.2, U1.27 (GPIO0/BOOT); also elsewhere on the board
enc_scl: U1.7 (GPIO7/TOUCH7/ADC1_CH6); also elsewhere on the board
enc_sda: U1.6 (GPIO6/TOUCH6/ADC1_CH5); also elsewhere on the board
gpio3: J4.16, U1.30 (SPIDQS/GPIO37/FSPIQ/SUBSPIQ); also elsewhere on the board
gpio4: J4.12, U1.28 (SPIIO6/GPIO35/FSPID/SUBSPID); also elsewhere on the board
gpio7: J4.13, U1.29 (SPIIO7/GPIO36/FSPICLK/SUBSPICLK); also elsewhere on the board
gpio8: J4.18, U1.31 (GPIO38/FSPIWP/SUBSPIWP); also elsewhere on the board
gpio9: J4.7, U1.37 (U0TXD/GPIO43/CLK_OUT1); also elsewhere on the board
gpio38: J4.24, JP2.2 (B), U1.23 (GPIO21); also elsewhere on the board
gpio39: J4.21, U1.32 (MTCK/GPIO39/CLK_OUT3/SUBSPICS1); also elsewhere on the board
gpio40: J4.23, U1.33 (MTDO/GPIO40/CLK_OUT2); also elsewhere on the board
gpio41: J4.22, U1.24 (GPIO47/SPICLK_P/SUBSPICLK_P_DIFF); also elsewhere on the board
gpio42: J4.19, U1.25 (GPIO48/SPICLK_N/SUBSPICLK_N_DIFF); also elsewhere on the board
gpio43: J4.8, U1.36 (U0RXD/GPIO44/CLK_OUT2); also elsewhere on the board
gpio44: J4.10, U1.34 (MTDI/GPIO41/CLK_OUT1); also elsewhere on the board
gpio47: J4.11, JP1.2 (B), U1.35 (MTMS/GPIO42); also elsewhere on the board
hidden_scl: U1.22 (GPIO14/TOUCH14/ADC2_CH3/FSPIWP/FSPIDQS/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); also elsewhere on the board
hidden_sda: U1.21 (GPIO13/TOUCH13/ADC2_CH2/FSPIQ/FSPIIO7/S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); also elsewhere on the board
m1_EN: U1.9 (GPIO16/U0CTS/ADC2_CH5/XTAL_32K_N); also elsewhere on the board
m1_PH: U1.8 (GPIO15/U0RTS/ADC2_CH4/XTAL_32K_P); also elsewhere on the board
m1_enc_cs: U1.5 (GPIO5/TOUCH5/ADC1_CH4); also elsewhere on the board
m2_EN: U1.11 (GPIO18/U1RXD/ADC2_CH7/CLK_OUT3); also elsewhere on the board
m2_PH: U1.10 (GPIO17/U1TXD/ADC2_CH6); also elsewhere on the board
m2_enc_cs: U1.4 (GPIO4/TOUCH4/ADC1_CH3); also elsewhere on the board
m3_EN: U1.15 (GPIO3/TOUCH3/ADC1_CH2); also elsewhere on the board
m3_PH: U1.12 (GPIO8/TOUCH8/ADC1_CH7/SUBSPICS1); also elsewhere on the board
m3_enc_cs: U1.17 (GPIO9/TOUCH9/ADC1_CH8/FSPIHD/SUBSPIHD); also elsewhere on the board
m4_EN: U1.19 (GPIO11/TOUCH11/ADC2_CH0/FSPID/FSPIIO5/S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); also elsewhere on the board
m4_PH: U1.18 (GPIO10/TOUCH10/ADC1_CH9/FSPICS0/FSPIIO4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); also elsewhere on the board
m4_enc_cs: U1.20 (GPIO12/TOUCH12/ADC2_CH1/FSPICLK/FSPIIO6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); also elsewhere on the board
p26: J4.26; also elsewhere on the board
p31: J4.31; also elsewhere on the board
p32: J4.32; also elsewhere on the board
p33: J4.33; also elsewhere on the board
p35: J4.35; also elsewhere on the board
p36: J4.36; also elsewhere on the board
p37: J4.37; also elsewhere on the board
p38: J4.38; also elsewhere on the board
p40: J4.40; also elsewhere on the board
reset: J3.1, R9.2, U1.3 (EN)
scl: J4.5, U1.39 (GPIO1/TOUCH1/ADC1_CH0); also elsewhere on the board
sda: J4.3, U1.38 (GPIO2/TOUCH2/ADC1_CH1); also elsewhere on the board
usb_d+: R6.1, U1.14 (GPIO20/U1CTS/ADC2_CH9/CLK_OUT1/USB_D+)
usb_d-: R7.1, U1.13 (GPIO19/U1RTS/ADC2_CH8/CLK_OUT2/USB_D-)

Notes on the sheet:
USB-C Programming connector
Motors
Power
Boot & reset
Indicators
The ADC2 Channels do not perform as expected with the wifi capabilities of the ESP32
Pass through pins
GPIO link to Rpi

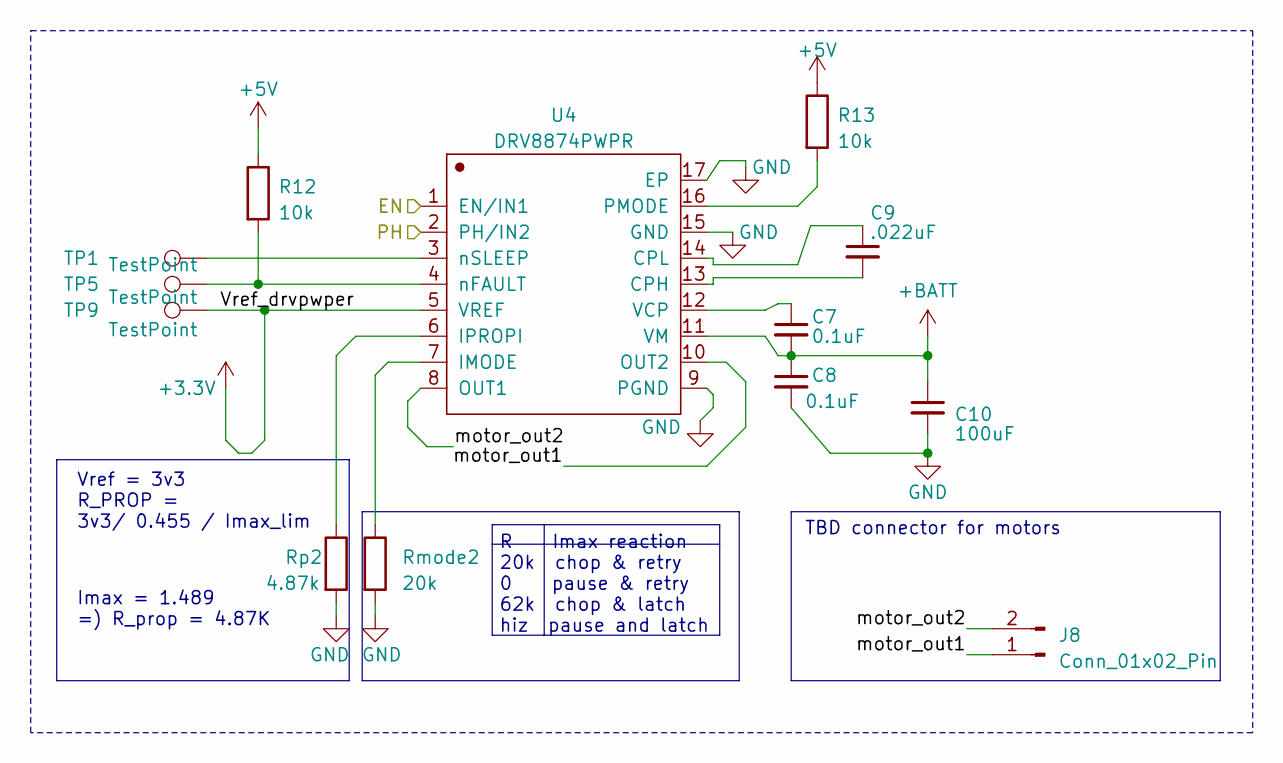
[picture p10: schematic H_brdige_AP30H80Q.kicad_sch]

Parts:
C7, C8: 0.1uF; C_0402_1005Metric; LCSC_Part_Number C3012377
C9: .022uF; C_0402_1005Metric; LCSC_Part_Number C380305
C10: 100uF; C_1210_3225Metric; LCSC_Part_Number C6120014
J8: Conn_01x02_Pin; PinHeader_1x02_P2.54mm_Vertical; LCSC_Part_Number C7430358
R12, R13: 10k; R_0402_1005Metric; LCSC_Part_Number C2906885
Rmode2: 20k; R_0402_1005Metric; LCSC_Part_Number C3017501
Rp2: 4.87k; R_0402_1005Metric; LCSC_Part_Number C3015971
TP1, TP5, TP9: TestPoint; TestPoint_Pad_1.0x1.0mm
U4: DRV8874PWPR; HTSSOP-16_L5.0-W4.4-P0.65-LS6.4-BL-EP; LCSC_Part_Number C1855818

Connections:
+3.3V: TP9.1, U4.5 (VREF); also elsewhere on the board
+5V: R12.1, R13.1; also elsewhere on the board
+BATT: C7.2, C8.1, C10.1, U4.11 (VM); also elsewhere on the board
/motor_controls1/motor_out1: J8.1, U4.10 (OUT2)
/motor_controls1/motor_out2: J8.2, U4.8 (OUT1)
GND: C8.2, C10.2, Rmode2.2, Rp2.2, U4.9 (PGND), U4.15 (GND), U4.17 (EP); also elsewhere on the board
unnamed: C9.2, U4.13 (CPH)
unnamed: C9.1, U4.14 (CPL)
unnamed: Rmode2.1, U4.7 (IMODE)
unnamed: Rp2.1, U4.6 (IPROPI)
unnamed: R13.2, U4.16 (PMODE)
unnamed: C7.1, U4.12 (VCP)
m1_EN: U4.1 (EN/IN1); also elsewhere on the board
m1_PH: U4.2 (PH/IN2); also elsewhere on the board

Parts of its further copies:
C3, C4, C11, C12, C26, C27: 0.1uF; C_0402_1005Metric; LCSC_Part_Number C3012377
C5, C13, C28: .022uF; C_0402_1005Metric; LCSC_Part_Number C380305
C6, C14, C29: 100uF; C_1210_3225Metric; LCSC_Part_Number C6120014
J6, J10, J22: Conn_01x02_Pin; PinHeader_1x02_P2.54mm_Vertical; LCSC_Part_Number C7430358
R10, R11, R14, R15, R36, R37: 10k; R_0402_1005Metric; LCSC_Part_Number C2906885
Rmode1, Rmode3, Rmode4: 20k; R_0402_1005Metric; LCSC_Part_Number C3017501
Rp1, Rp3, Rp4: 4.87k; R_0402_1005Metric; LCSC_Part_Number C3015971
TP2, TP3, TP4, TP6, TP7, TP8, TP10, TP11, TP12: TestPoint; TestPoint_Pad_1.0x1.0mm
U3, U5, U9: DRV8874PWPR; HTSSOP-16_L5.0-W4.4-P0.65-LS6.4-BL-EP; LCSC_Part_Number C1855818

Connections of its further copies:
+3.3V: TP10.1, TP11.1, TP12.1, U3.5 (VREF), U5.5 (VREF), U9.5 (VREF); also elsewhere on the board
+5V: R10.1, R11.1, R14.1, R15.1, R36.1, R37.1; also elsewhere on the board
+BATT: C3.2, C4.1, C6.1, C11.2, C12.1, C14.1, C26.2, C27.1, C29.1, U3.11 (VM), U5.11 (VM), U9.11 (VM); also elsewhere on the board
/motor_controls2/motor_out1: J6.1, U3.10 (OUT2)
/motor_controls2/motor_out2: J6.2, U3.8 (OUT1)
/motor_controls3/motor_out1: J10.1, U5.10 (OUT2)
/motor_controls3/motor_out2: J10.2, U5.8 (OUT1)
/motor_controls4/motor_out1: J22.1, U9.10 (OUT2)
/motor_controls4/motor_out2: J22.2, U9.8 (OUT1)
GND: C4.2, C6.2, C12.2, C14.2, C27.2, C29.2, Rmode1.2, Rmode3.2, Rmode4.2, Rp1.2, Rp3.2, Rp4.2, U3.9 (PGND), U3.15 (GND), U3.17 (EP), U5.9 (PGND), U5.15 (GND), U5.17 (EP), U9.9 (PGND), U9.15 (GND), U9.17 (EP); also elsewhere on the board
unnamed: C5.2, U3.13 (CPH)
unnamed: C5.1, U3.14 (CPL)
unnamed: Rmode1.1, U3.7 (IMODE)
unnamed: Rp1.1, U3.6 (IPROPI)
unnamed: R11.2, U3.16 (PMODE)
unnamed: C3.1, U3.12 (VCP)
unnamed: C13.2, U5.13 (CPH)
unnamed: C13.1, U5.14 (CPL)
unnamed: Rmode3.1, U5.7 (IMODE)
unnamed: Rp3.1, U5.6 (IPROPI)
unnamed: R15.2, U5.16 (PMODE)
unnamed: C11.1, U5.12 (VCP)
unnamed: R14.2, TP7.1, U5.4 (nFAULT)
unnamed: TP3.1, U5.3 (nSLEEP)
unnamed: C28.2, U9.13 (CPH)
unnamed: C28.1, U9.14 (CPL)
unnamed: Rmode4.1, U9.7 (IMODE)
unnamed: Rp4.1, U9.6 (IPROPI)
unnamed: R37.2, U9.16 (PMODE)
unnamed: C26.1, U9.12 (VCP)
unnamed: R36.2, TP8.1, U9.4 (nFAULT)
unnamed: TP4.1, U9.3 (nSLEEP)
m2_EN: U3.1 (EN/IN1); also elsewhere on the board
m2_PH: U3.2 (PH/IN2); also elsewhere on the board
m3_EN: U5.1 (EN/IN1); also elsewhere on the board
m3_PH: U5.2 (PH/IN2); also elsewhere on the board
m4_EN: U9.1 (EN/IN1); also elsewhere on the board
m4_PH: U9.2 (PH/IN2); also elsewhere on the board

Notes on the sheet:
Vref = 3v3 R_PROP = 3v3/ 0.455 / Imax_lim
TBD connector for motors
Imax = 1.489 =) R_prop = 4.87K
R Imax reaction 20k chop & retry 0 pause & retry 62k chop & latch hiz pause and latch

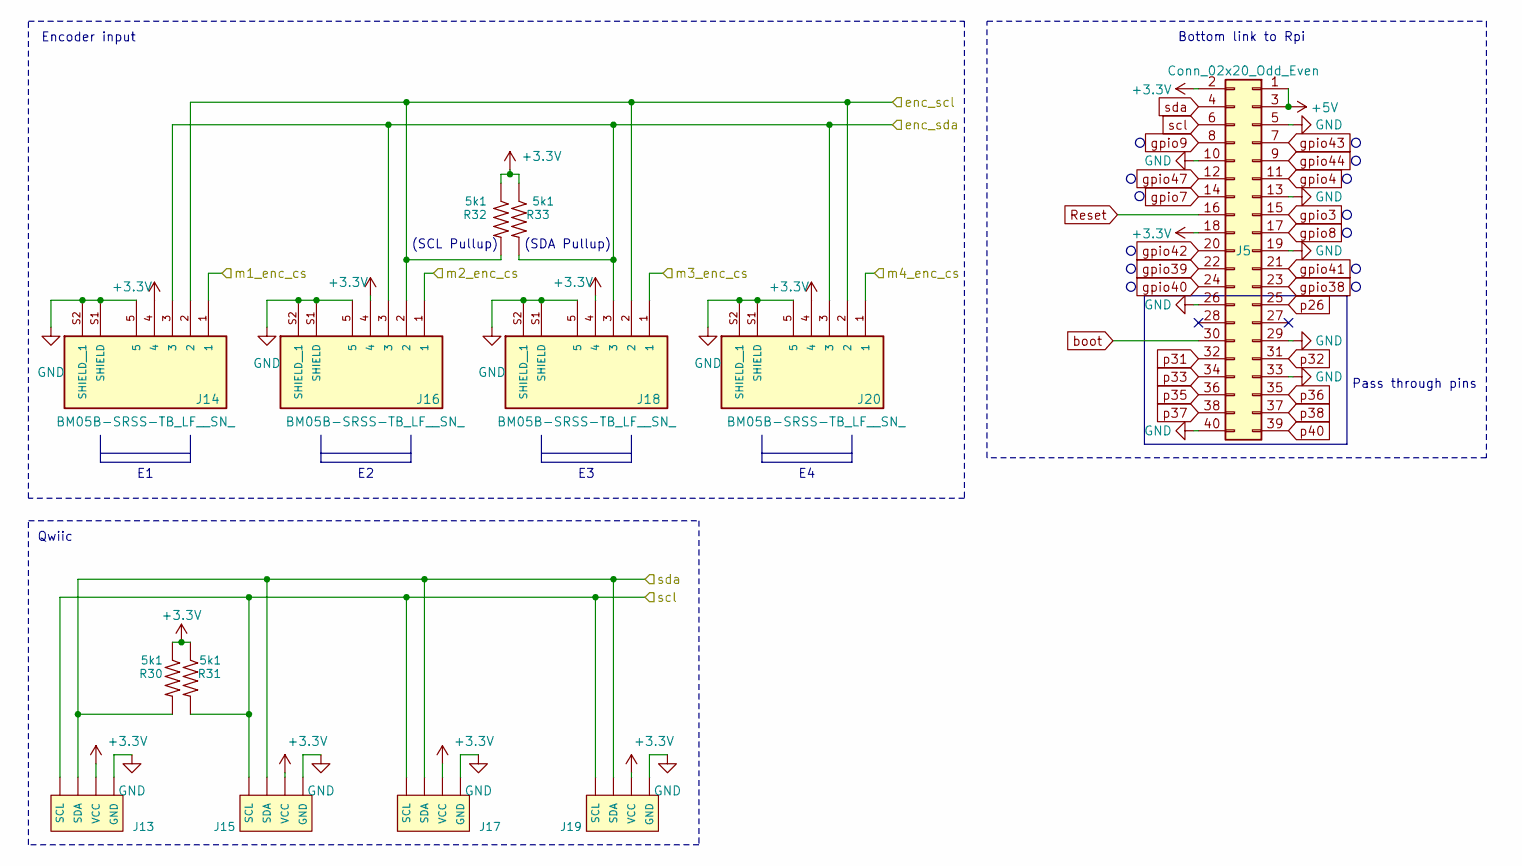
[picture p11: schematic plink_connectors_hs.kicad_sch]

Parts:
J5: Conn_02x20_Odd_Even; PinSocket_2x20_P2.54mm_Vertical_SMD; LCSC_Part_Number C3975165
J13, J15, J17, J19: I2C_STANDARDQWIIC; JST_SH_BM04B-SRSS-TB_1x04-1MP_P1.00mm_Vertical; LCSC_Part_Number C160404
J14, J16, J18, J20: BM05B-SRSS-TB_LF__SN_; JST_BM05B-SRSS-TB_LF__SN_; PARTREV N/A; LCSC_Part_Number C265092
R30, R31, R32, R33: 5k1; R_0402_1005Metric; LCSC_Part_Number C409700

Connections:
+3.3V: J5.2, J5.18, J13.2 (VCC), J14.4, J15.2 (VCC), J16.4, J17.2 (VCC), J18.4, J19.2 (VCC), J20.4, R30.1, R31.1, R32.1, R33.1; also elsewhere on the board
+5V: J5.1, J5.3; also elsewhere on the board
GND: J5.5, J5.10, J5.13, J5.19, J5.26, J5.29, J5.33, J5.40, J13.1 (GND), J14.5, J14.S1 (SHIELD), J14.S2 (SHIELD__1), J15.1 (GND), J16.5, J16.S1 (SHIELD), J16.S2 (SHIELD__1), J17.1 (GND), J18.5, J18.S1 (SHIELD), J18.S2 (SHIELD__1), J19.1 (GND), J20.5, J20.S1 (SHIELD), J20.S2 (SHIELD__1); also elsewhere on the board
Reset: J5.16; also elsewhere on the board
boot: J5.30; also elsewhere on the board
enc_scl: J14.2, J16.2, J18.2, J20.2, R32.2; also elsewhere on the board
enc_sda: J14.3, J16.3, J18.3, J20.3, R33.2; also elsewhere on the board
gpio3: J5.15; also elsewhere on the board
gpio4: J5.11; also elsewhere on the board
gpio7: J5.14; also elsewhere on the board
gpio8: J5.17; also elsewhere on the board
gpio9: J5.8; also elsewhere on the board
gpio38: J5.23; also elsewhere on the board
gpio39: J5.22; also elsewhere on the board
gpio40: J5.24; also elsewhere on the board
gpio41: J5.21; also elsewhere on the board
gpio42: J5.20; also elsewhere on the board
gpio43: J5.7; also elsewhere on the board
gpio44: J5.9; also elsewhere on the board
gpio47: J5.12; also elsewhere on the board
m1_enc_cs: J14.1; also elsewhere on the board
m2_enc_cs: J16.1; also elsewhere on the board
m3_enc_cs: J18.1; also elsewhere on the board
m4_enc_cs: J20.1; also elsewhere on the board
p26: J5.25; also elsewhere on the board
p31: J5.32; also elsewhere on the board
p32: J5.31; also elsewhere on the board
p33: J5.34; also elsewhere on the board
p35: J5.36; also elsewhere on the board
p36: J5.35; also elsewhere on the board
p37: J5.38; also elsewhere on the board
p38: J5.37; also elsewhere on the board
p40: J5.39; also elsewhere on the board
scl: J5.6, J13.4 (SCL), J15.4 (SCL), J17.4 (SCL), J19.4 (SCL), R31.2; also elsewhere on the board
sda: J5.4, J13.3 (SDA), J15.3 (SDA), J17.3 (SDA), J19.3 (SDA), R30.2; also elsewhere on the board

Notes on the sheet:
Qwiic
Bottom link to Rpi
Encoder input
(SCL Pullup)
Pass through pins
(SDA Pullup)

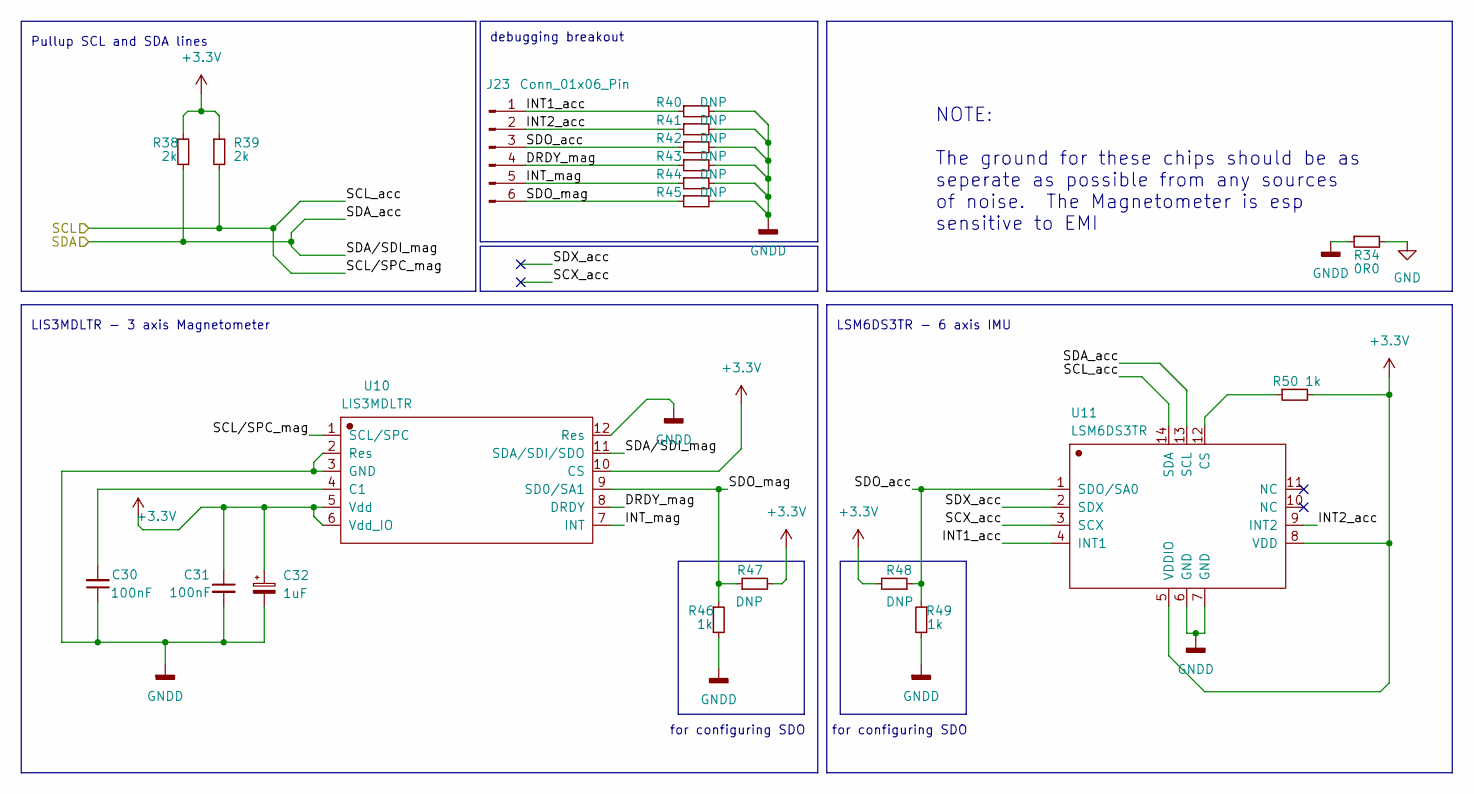
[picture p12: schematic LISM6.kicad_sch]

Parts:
C30, C31: 100nF; C_0402_1005Metric; LCSC_Part_Number C880603
C32: 1uF; C_0603_1608Metric; LCSC_Part_Number C15849
J23: Conn_01x06_Pin; PinHeader_1x06_P1.00mm_Vertical; LCSC_Part_Number C7434639
R34: 0R0; R_0603_1608Metric; LCSC_Part_Number C2906858
R38, R39: 2k; R_0402_1005Metric; LCSC_Part_Number C4109
R40, R41, R42, R43, R44, R45, R47, R48: DNP; R_0402_1005Metric
R46, R49, R50: 1k; R_0402_1005Metric; LCSC_Part_Number C2906899
U10: LIS3MDLTR; LIS3MDLTR_LGA-12; LCSC_Part_Number C478483
U11: LSM6DS3TR; LSM6DSOTR_LGA-14; LCSC_Part_Number C95230

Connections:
+3.3V: C31.1, C32.1, R38.1, R39.1, R47.2, R48.2, R50.2, U10.5 (Vdd), U10.6 (Vdd_IO), U10.10 (CS), U11.5 (VDDIO), U11.8 (VDD); also elsewhere on the board
/IMU 6 + 3/DRDY_mag: J23.4, R43.1, U10.8 (DRDY)
/IMU 6 + 3/INT1_acc: J23.1, R40.1, U11.4 (INT1)
/IMU 6 + 3/INT2_acc: J23.2, R41.1, U11.9 (INT2)
/IMU 6 + 3/INT_mag: J23.5, R44.1, U10.7 (INT)
/IMU 6 + 3/SCX_acc: U11.3 (SCX)
/IMU 6 + 3/SDO_acc: J23.3, R42.1, R48.1, R49.1, U11.1 (SDO/SA0)
/IMU 6 + 3/SDO_mag: J23.6, R45.1, R46.1, R47.1, U10.9 (SD0/SA1)
/IMU 6 + 3/SDX_acc: U11.2 (SDX)
GND: R34.2; also elsewhere on the board
GNDD: C30.1, C31.2, C32.2, R34.1, R40.2, R41.2, R42.2, R43.2, R44.2, R45.2, R46.2, R49.2, U10.2 (Res), U10.3 (GND), U10.12 (Res), U11.6 (GND), U11.7 (GND)
unnamed: C30.2, U10.4 (C1)
unnamed: R50.1, U11.12 (CS)
hidden_scl: R39.2, U10.1 (SCL/SPC), U11.14 (SDA); also elsewhere on the board
hidden_sda: R38.2, U10.11 (SDA/SDI/SDO), U11.13 (SCL); also elsewhere on the board

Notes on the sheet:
NOTE: The ground for these chips should be as seperate as possible from any sources of noise. The Magnetometer is esp sensitive to EMI
debugging breakout
for configuring SDO
LSM6DS3TR - 6 axis IMU
Pullup SCL and SDA lines
LIS3MDLTR - 3 axis Magnetometer

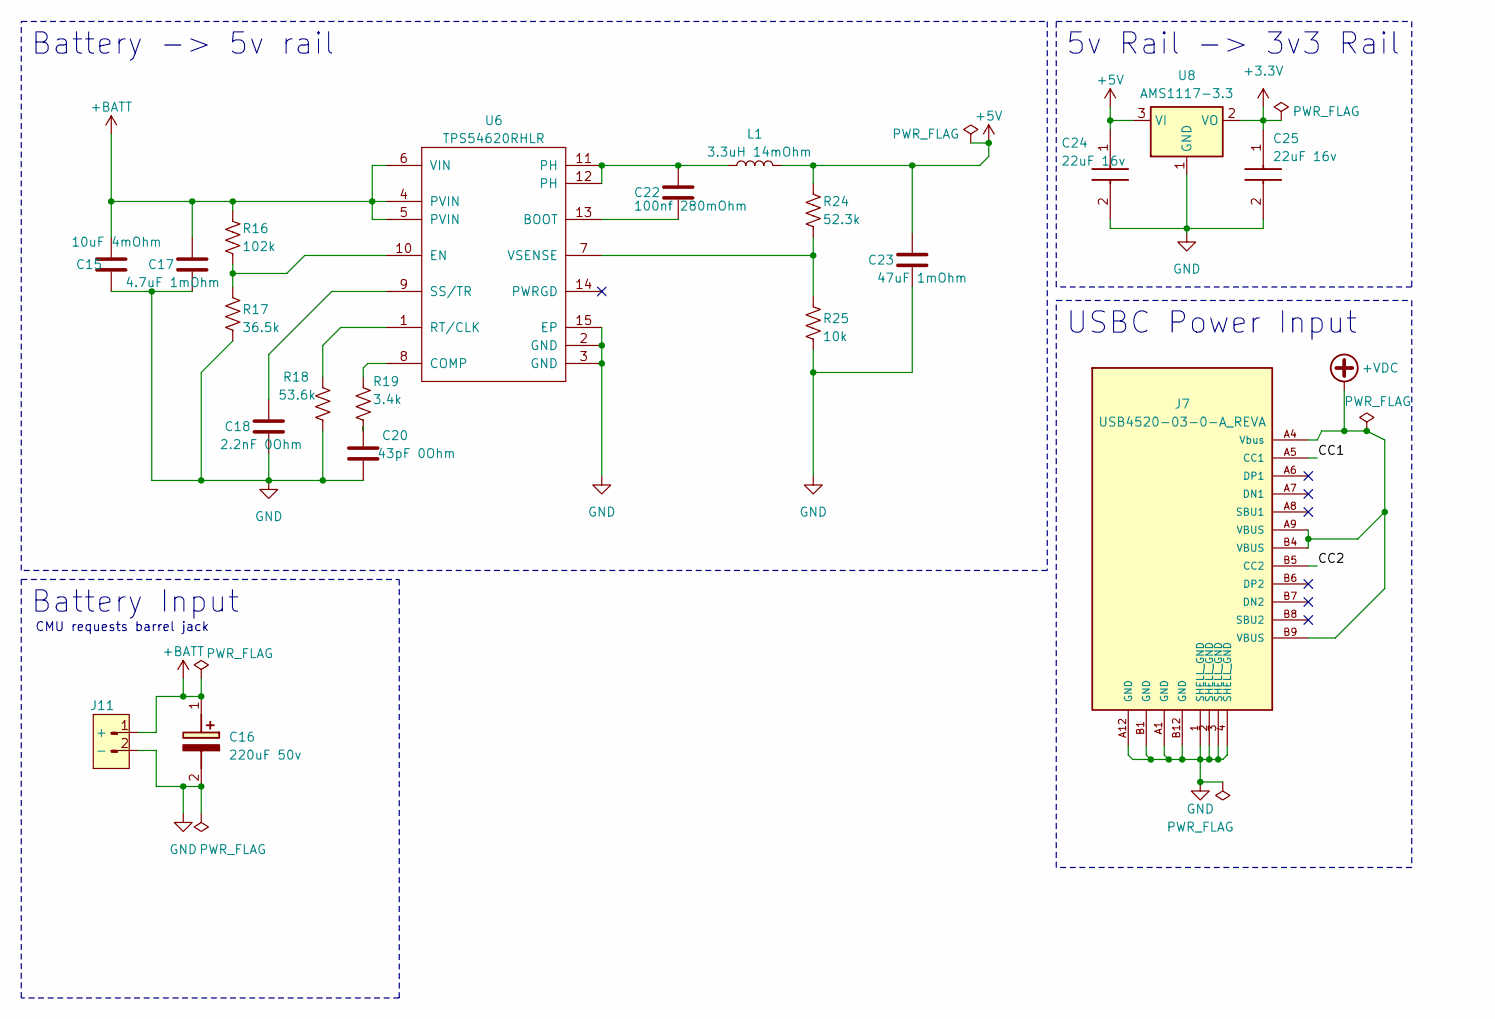
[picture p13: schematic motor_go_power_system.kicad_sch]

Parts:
C15: 10uF 4mOhm; C_0805_2012Metric; LCSC_Part_Number C5448891
C16: 220uF 50v; CP_Elec_10x10; Mouser Part Number 140-RGA221M1EBK0811G
C17: 4.7uF 1mOhm; C_0603_1608Metric; LCSC_Part_Number C6119856
C18: 2.2nF 0Ohm; C_0201_0603Metric; LCSC_Part_Number C285033
C20: 43pF 0Ohm; C_0201_0603Metric; LCSC_Part_Number C3037638
C22: 100nf 280mOhm; C_0402_1005Metric; LCSC_Part_Number C880603
C23: 47uF 1mOhm; C_1210_3225Metric; LCSC_Part_Number C7432791
C24, C25: 22uF 16v; C_0603_1608Metric; Mouser Part Number 187-CL21A226MQQNNNE
J7: USB4520-03-0-A_REVA; USB-C-SMD_TYPEC-303-ACP16; LCSC_Part_Number C720628
J11: CONN-TH_DC-005-2.5A-2.0; LCSC_Part_Number C319099
L1: 3.3uH 14mOhm; IND-SMD_L7.3-W6.6; LCSC_Part_Number C2847540
R16: 102k; R_0402_1005Metric; LCSC_Part_Number C2933066
R17: 36.5k; R_0402_1005Metric; LCSC_Part_Number C25887
R18: 53.6k; R_0402_1005Metric; LCSC_Part_Number C5153961
R19: 3.4k; R_0402_1005Metric; LCSC_Part_Number C3013164
R24: 52.3k; R_0402_1005Metric; LCSC_Part_Number C2998086
R25: 10k; R_0402_1005Metric; LCSC_Part_Number C2906885
U6: TPS54620RHLR; VQFN-14_L3.5-W3.5-P0.50-TL-EP_TPS54622RHLT; LCSC_Part_Number C263274
U8: AMS1117-3.3; SOT-223-3_TabPin2; LCSC_Part_Number C347222

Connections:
+3.3V: C25.1, U8.2 (VO); also elsewhere on the board
+5V: C23.1, C24.1, L1.2, R24.1, U8.3 (VI); also elsewhere on the board
+BATT: C15.1, C16.1 (+), C17.1, J11.1 (+), R16.1, U6.4 (PVIN), U6.5 (PVIN), U6.6 (VIN); also elsewhere on the board
+VDC: J7.A4 (Vbus), J7.A9 (VBUS), J7.B4 (VBUS), J7.B9 (VBUS); also elsewhere on the board
/Power Reg and Dist/CC1: J7.A5 (CC1); also elsewhere on the board
/Power Reg and Dist/CC2: J7.B5 (CC2); also elsewhere on the board
GND: C15.2, C16.2 (-), C17.2, C18.2, C20.2, C23.2, C24.2, C25.2, J7.1 (SHELL_GND), J7.2 (SHELL_GND), J7.3 (SHELL_GND), J7.4 (SHELL_GND), J7.A1 (GND), J7.A12 (GND), J7.B1 (GND), J7.B12 (GND), J11.2 (-), R17.2, R18.2, R25.2, U6.2 (GND), U6.3 (GND), U6.15 (EP), U8.1 (GND); also elsewhere on the board
unnamed: C20.1, R19.2
unnamed: C22.1, L1.1, U6.11 (PH), U6.12 (PH)
unnamed: C22.2, U6.13 (BOOT)
unnamed: R19.1, U6.8 (COMP)
unnamed: R16.2, R17.1, U6.10 (EN)
unnamed: R18.1, U6.1 (RT/CLK)
unnamed: C18.1, U6.9 (SS/TR)
unnamed: R24.2, R25.1, U6.7 (VSENSE)

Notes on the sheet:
USBC Power Input
Battery -> 5v rail
CMU requests barrel jack
Battery Input
5v Rail -> 3v3 Rail

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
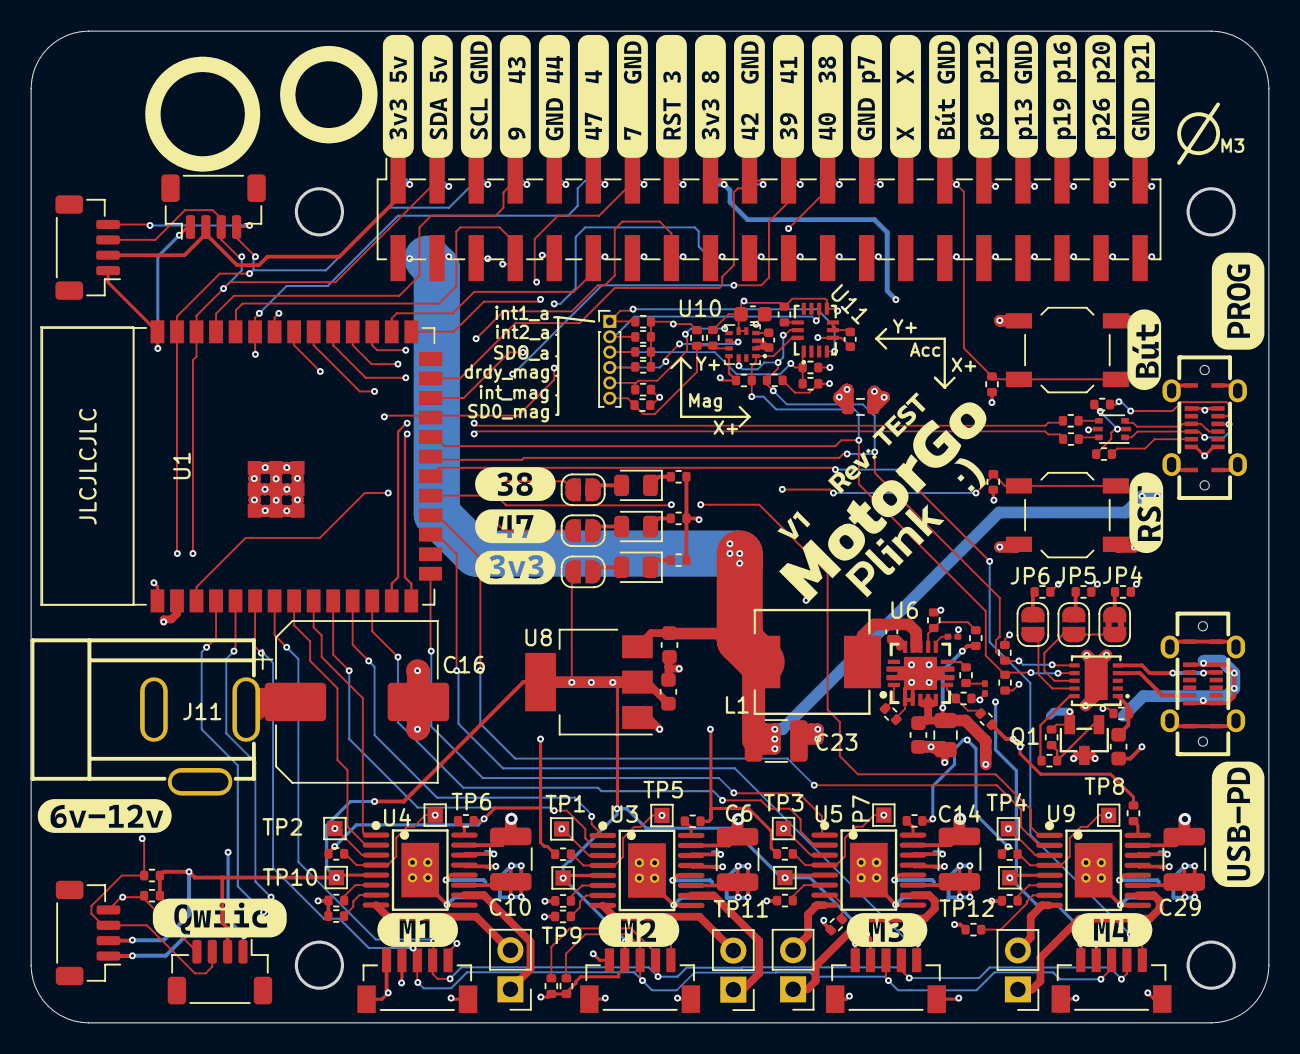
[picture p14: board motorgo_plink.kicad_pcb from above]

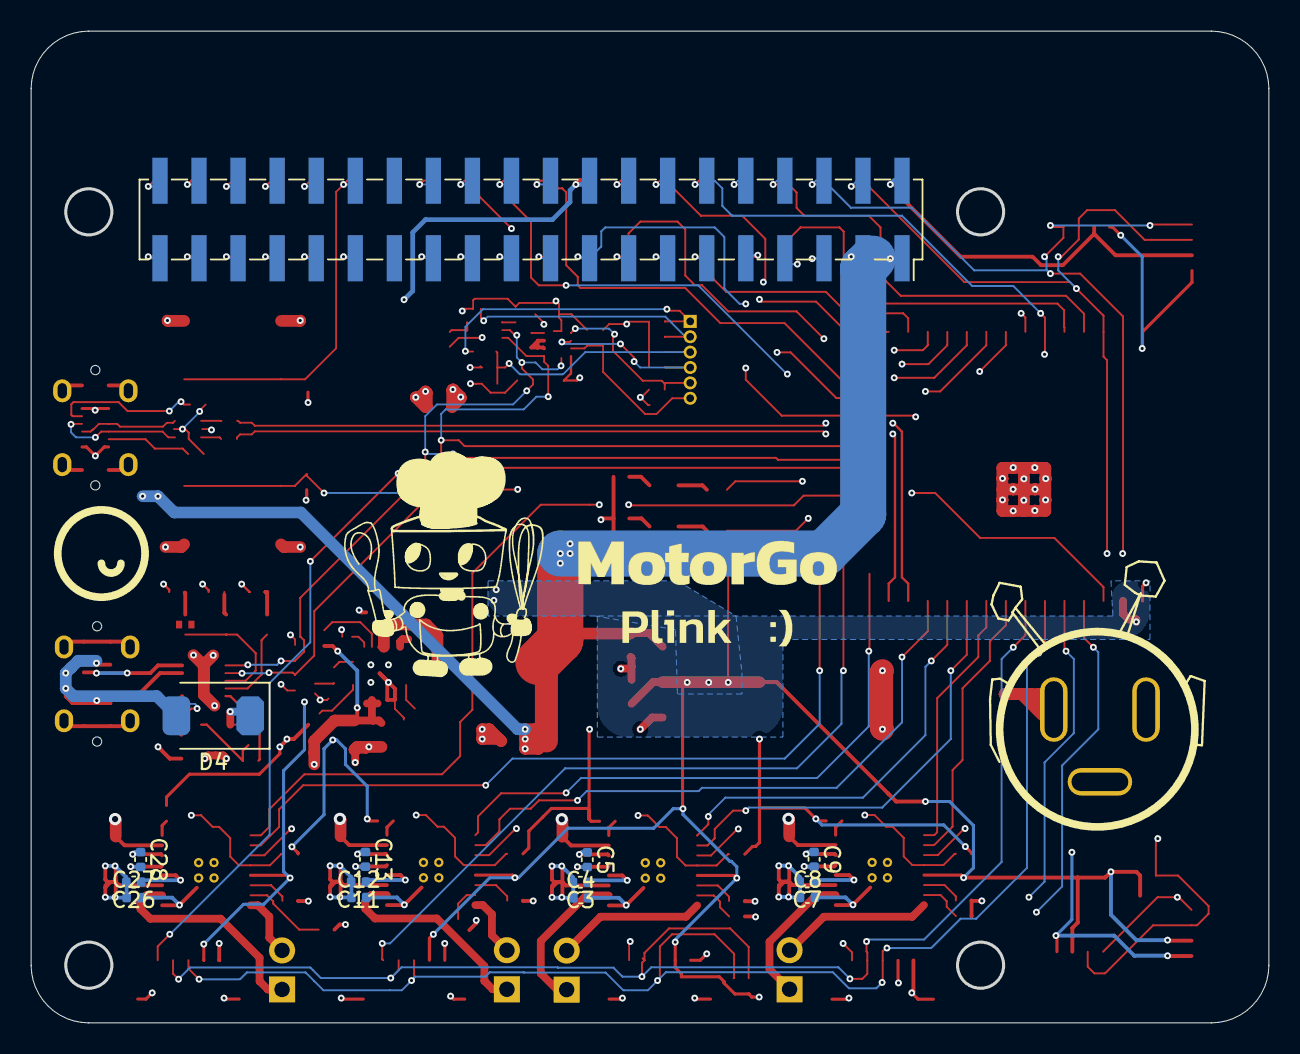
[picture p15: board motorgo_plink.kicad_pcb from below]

Board: 4 copper layers, 80.5 x 64.5 mm, 141 parts (14 on the bottom side), 130 nets.

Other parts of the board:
C21: 1uF; C_0603_1608Metric
D4: 20V 5A; D_SMB_LCSC_C5366311
JP4: SolderJumper_2_Bridged; SolderJumper-2_P1.3mm_Bridged2Bar_RoundedPad1.0x1.5mm
JP5, JP6: SolderJumper_2_Open; SolderJumper-2_P1.3mm_Open_RoundedPad1.0x1.5mm
Q1: SI2323; SI2323_SOT-23-3_L2.9-W1.3-P0.95-LS2.4-BR
R20: 10R 1%; R_0402_1005Metric
R21, R22: DNP; R_0402_1005Metric
R23: 5.1K; R_0402_1005Metric
R26: 49.9K; R_0402_1005Metric
R27: 10K; R_0402_1005Metric
R28: 14K; R_0402_1005Metric
R29: 10.5K; R_0402_1005Metric
U7: HUSB238_002DD; DFN-10_L3.0-W3.0-P0.50-BL-EP2.5

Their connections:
+3.3V: R21.1, R22.1; also elsewhere on the board
+BATT: Q1.3 (D); also elsewhere on the board
+VDC: D4.2 (A), R20.1; also elsewhere on the board
/Power Reg and Dist/CC1: U7.4 (CC1); also elsewhere on the board
/Power Reg and Dist/CC2: U7.5 (CC2); also elsewhere on the board
GND: C21.2, R27.2, R28.2, R29.2, U7.11 (GND); also elsewhere on the board
unnamed: D4.1 (K), Q1.2 (S), R26.1
unnamed: JP4.1 (A), R27.1
unnamed: JP4.2 (B), JP5.2 (B), U7.8 (VSET)
unnamed: JP5.1 (A), R28.1
unnamed: JP6.1 (A), R29.1
unnamed: JP6.2 (B), U7.9 (ISET)
unnamed: Q1.1 (G), R23.2, R26.2
unnamed: R23.1, U7.10 (GATE)
unnamed: C21.1, R20.2, U7.1 (VIN)
hidden_scl: R22.2, U7.7 (SCL); also elsewhere on the board
hidden_sda: R21.2, U7.6 (SDA); also elsewhere on the board

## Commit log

2024-05-22 first commit with base project
    [H_brdige_AP30H80Q.kicad_sch, LISM6.kicad_sch, gopherMezz.kicad_sch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]
2024-05-22 added board blank file
2024-05-28 WIP update for BOM co-work
    [H_brdige_AP30H80Q.kicad_sch, LISM6.kicad_sch]
2024-05-29 WIP update, schematic mainly complete
    [H_brdige_AP30H80Q.kicad_sch, LISM6.kicad_sch, motor_go_power_system.kicad_sch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]
2024-05-30 WIP update. Parts semi-finalized
    [H_brdige_AP30H80Q.kicad_sch, LISM6.kicad_sch, motor_go_power_system.kicad_sch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]
2024-05-30 WIP update. Layout begin
    [H_brdige_AP30H80Q.kicad_sch, LISM6.kicad_sch, motor_go_power_system.kicad_sch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]
2024-05-31 WIP update. Ready for BOM editing
    [H_brdige_AP30H80Q.kicad_sch, LISM6.kicad_sch, motor_go_power_system.kicad_sch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]
2024-06-02 WIP update. change USBC port
    [H_brdige_AP30H80Q.kicad_sch, LISM6.kicad_sch, motor_go_power_system.kicad_sch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]
2024-06-03 ready for order
    [motorgo_plink.kicad_pcb, motorgo_plink.kicad_sch]
2024-06-03 fix DRC errors
    [motorgo_plink.kicad_pcb]
2024-06-03 WIP (TS) - updating BOM with values from other branch.
    [H_brdige_AP30H80Q.kicad_sch, LISM6.kicad_sch, motor_go_power_system.kicad_sch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]
2024-06-03 fix C31 and C30
    [motorgo_plink.kicad_pcb]
2024-06-03 updated BOM in prep for order - TS
    [H_brdige_AP30H80Q.kicad_sch, LISM6.kicad_sch, motor_go_power_system.kicad_sch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]
2024-06-04 added J11 p/n - TS
    [motor_go_power_system.kicad_sch]
2024-10-09 wip culling of non-vital schematic components
    [H_brdige_AP30H80Q.kicad_sch, LISM6.kicad_sch, motor_go_power_system.kicad_sch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]
2024-10-10 wip culling schematics and removing tracks
    [LISM6.kicad_sch, motor_go_power_system.kicad_sch, motorgo_plink.kicad_pcb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]
2024-10-14 wip schematic edits to account for buck reg design
    [DRV8825.kicad_sch, H_brdige_AP30H80Q.kicad_sch, motor_go_power_system.kicad_sch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]
2024-10-15 wip layout work begun, board dimensions finalized
    [DRV8825.kicad_sch, LISM6.kicad_sch, motor_go_power_system.kicad_sch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]
2024-10-16 layout complete! checkpoint ready for design review
    [motor_go_power_system.kicad_sch, motorgo_plink.kicad_pcb, motorgo_plink.kicad_sch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]
2024-10-16 silkscreen added and DRC satisfied
    [WBOperatingValuesDesign4.csv]
2024-10-17 production files and all edits for final send off of v1.0
    [DRV8825.kicad_sch, LISM6.kicad_sch, motor_go_power_system.kicad_sch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]
2024-10-17 added schematic pdf and removed vestigal files
2024-11-11 added schottky diode to local libraries
2024-11-11 added symbols and footprints to local libraries
2024-11-11 updated schematic to fix IMU i2c mismatch, silkscreen readability, schottky backpower diode, and added RC Servo pins
    [LISM6.kicad_sch, motor_go_power_system.kicad_sch, motorgo_plink.kicad_sch]
2024-11-11 updated git ignore to include cache files generated by kicad
2024-11-11 added soldermask on back of board for mounting holes
    [motorgo_plink.kicad_pcb]
